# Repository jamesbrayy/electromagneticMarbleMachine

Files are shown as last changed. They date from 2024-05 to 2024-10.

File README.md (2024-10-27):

# electromagneticMarbleMachine
 
a marble machine with a five-stage coil gun to accelerate the marbles.

optimised for ~300V charges (225 J) but capable of up to 405V to give a 10% safety margin (410.0625 J).

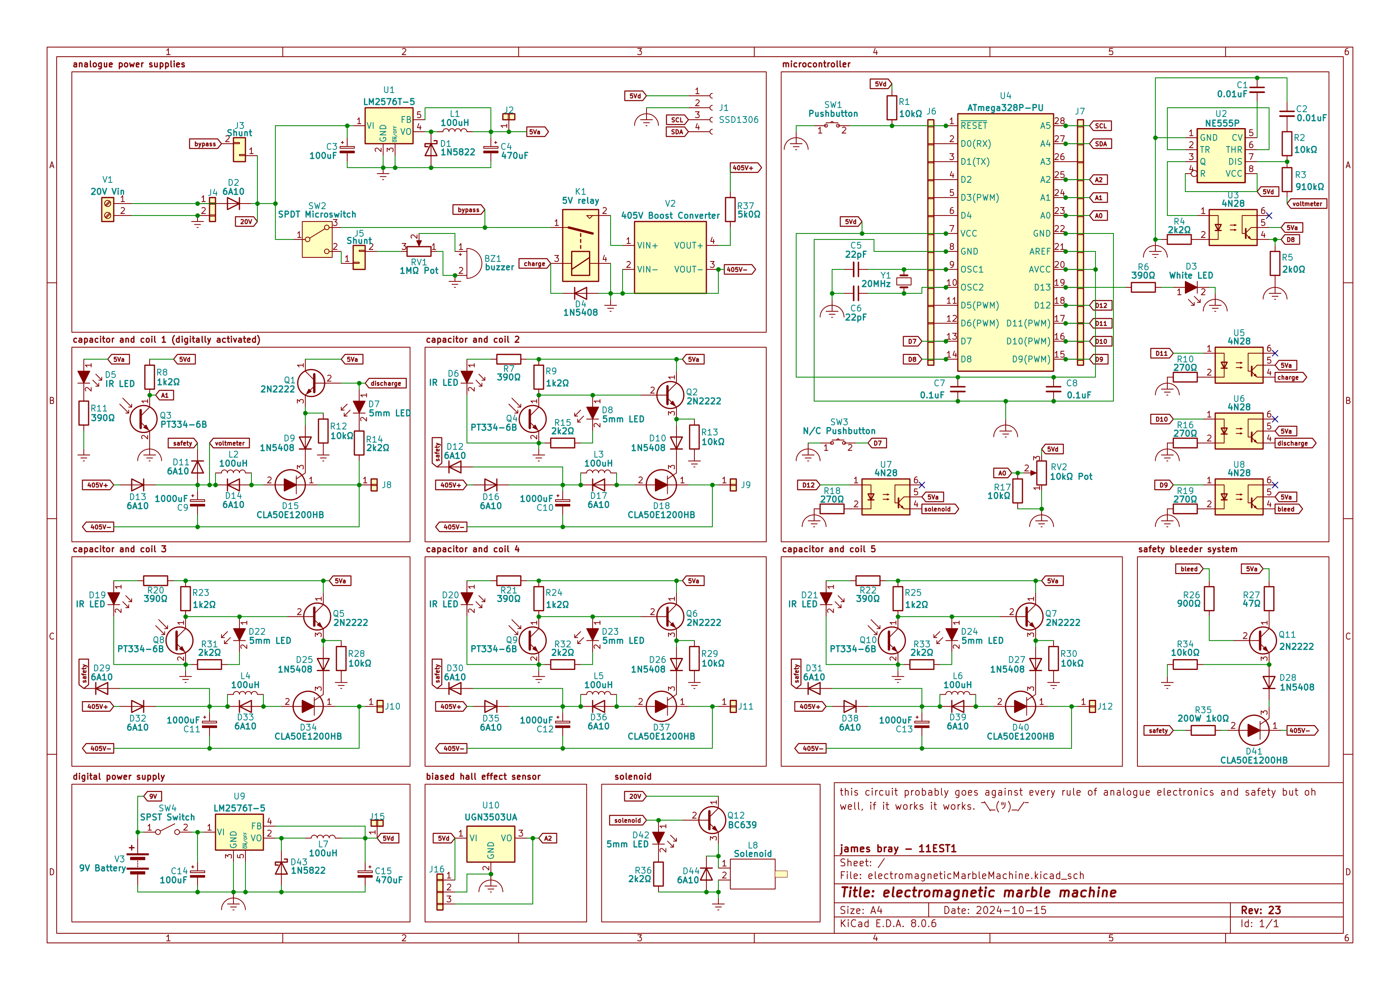
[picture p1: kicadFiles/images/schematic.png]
schematic image

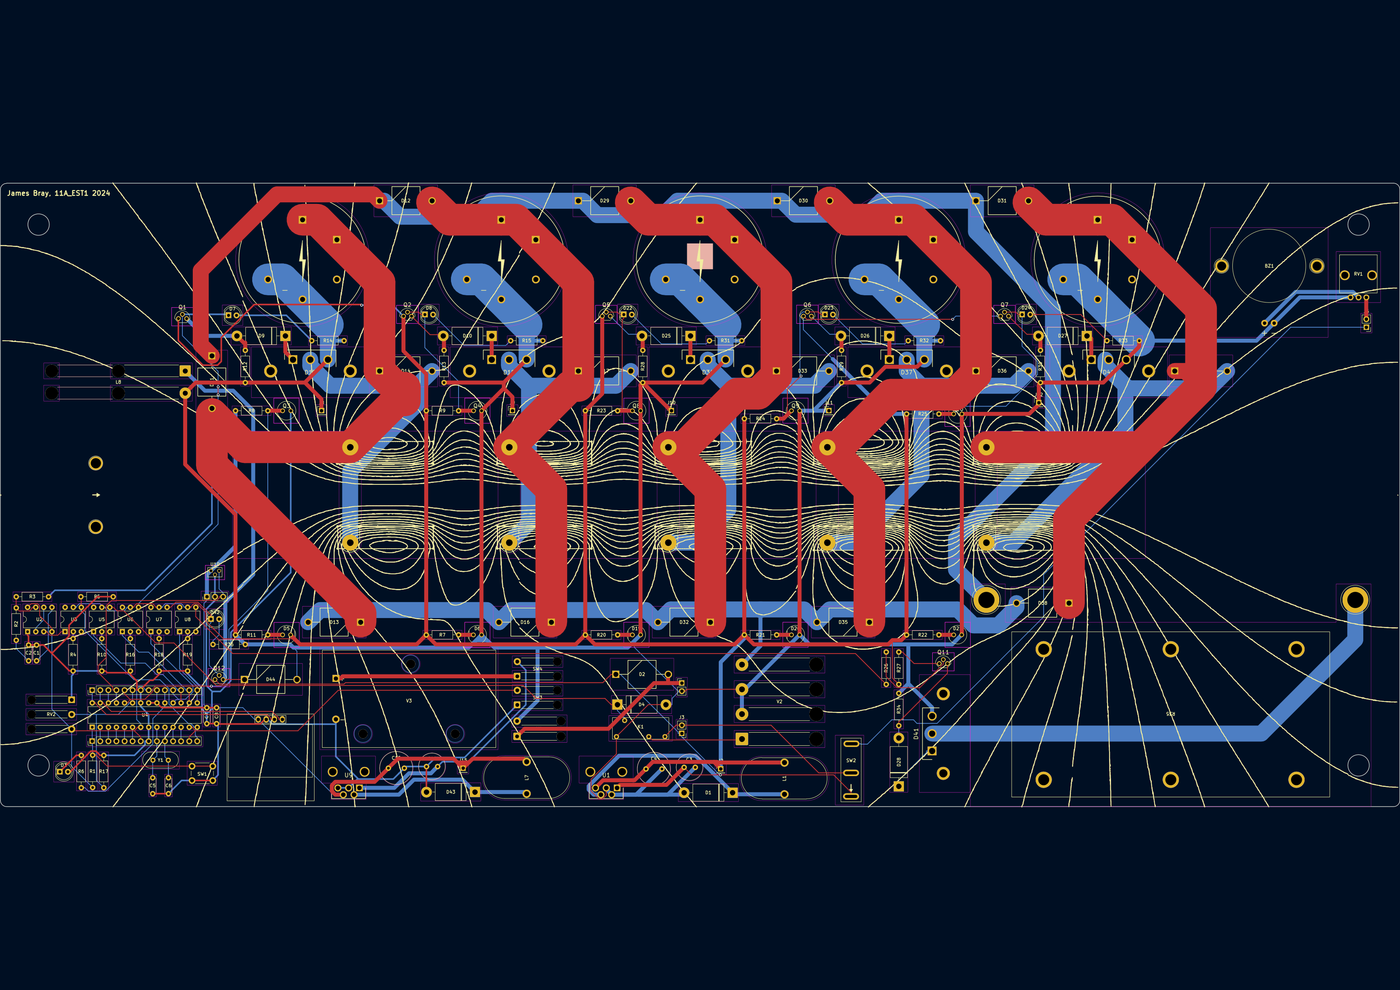
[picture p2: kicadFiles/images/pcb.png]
pcb image


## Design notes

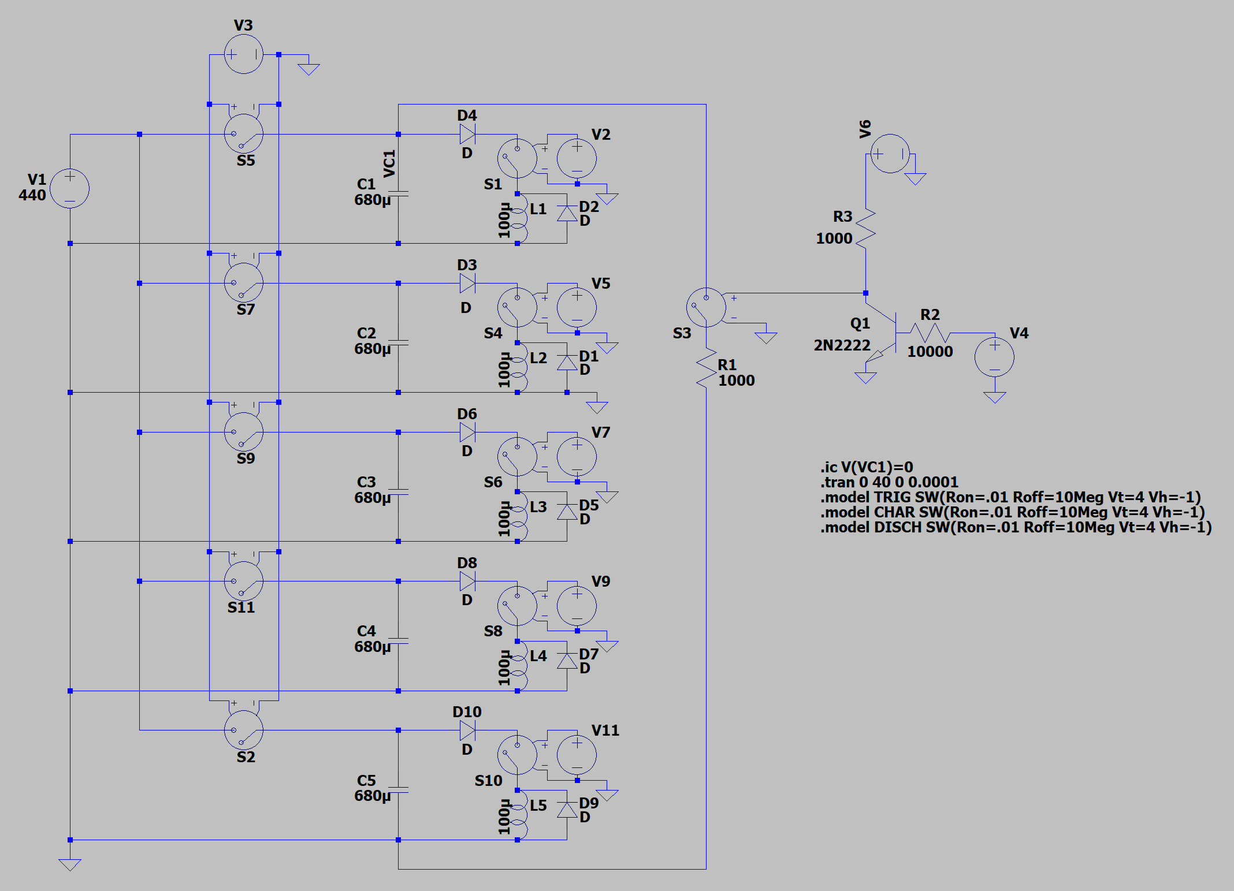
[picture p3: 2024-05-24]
simulationFiles/ltspice files/schematicSPICE.png

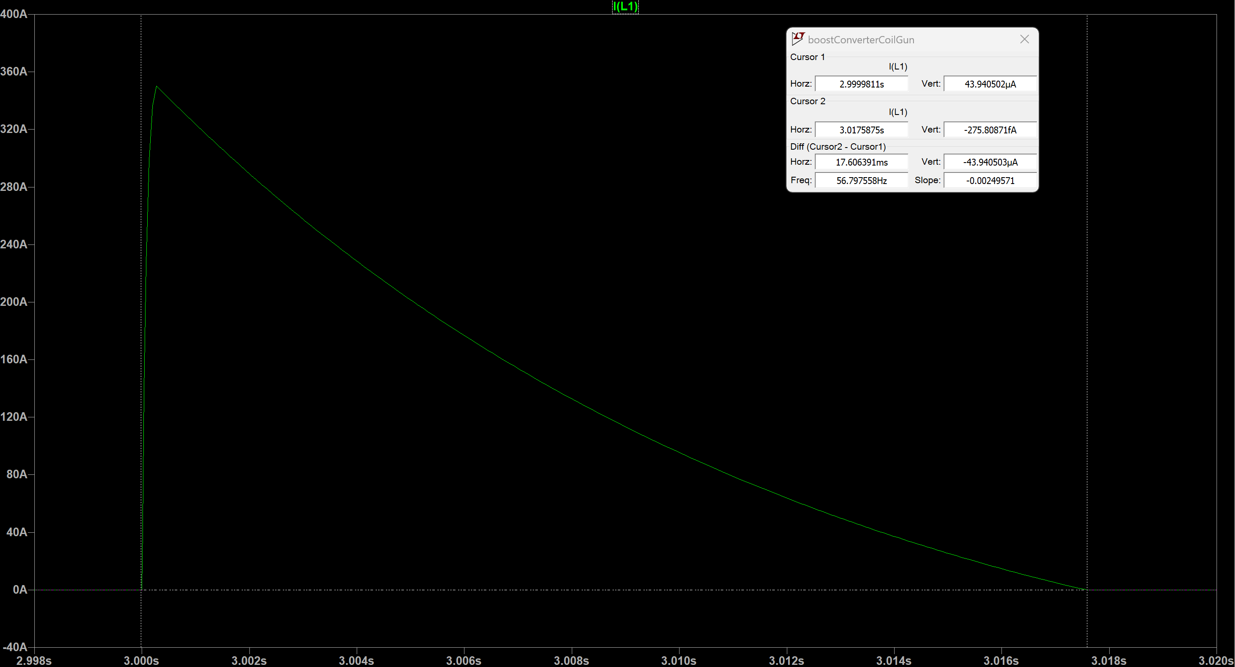
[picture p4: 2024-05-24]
simulationFiles/ltspice files/inductorPulse.png

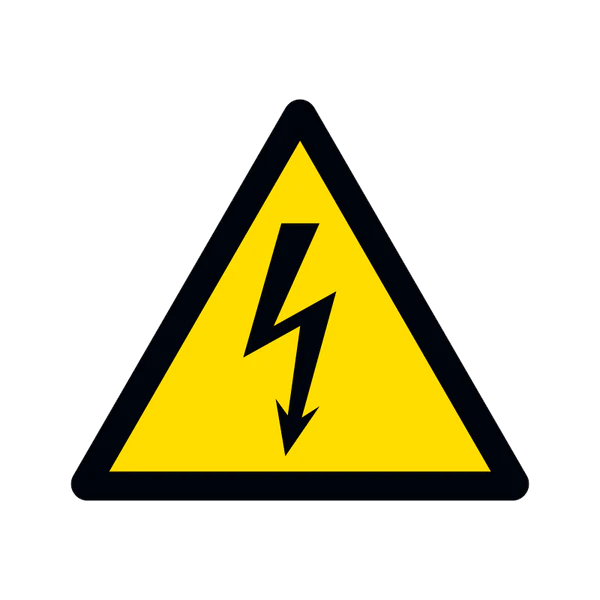
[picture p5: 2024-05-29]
simulationFiles/other random stuff/ruhRohRaggy.png

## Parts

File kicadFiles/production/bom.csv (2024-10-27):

Designator | Footprint | Quantity | Value | LCSC Part #
BZ1 | Buzzer | 1 | buzzer
C1, C2 | C_Disc_D4.3mm_W1.9mm_P5.00mm | 2 | 0.01uF
C10, C11, C12, C13, C9 | officialCAP | 5 | 1000uF
C14, C3 | C_Radial_D8.0mm_H11.5mm_P3.50mm | 2 | 100uF
C15, C4 | C_Radial_D10.0mm_H12.5mm_P5.00mm | 2 | 470uF
C5, C6 | C_Disc_D4.3mm_W1.9mm_P5.00mm | 2 | 22pF
C7, C8 | C_Disc_D4.3mm_W1.9mm_P5.00mm | 2 | 0.1uF
D1, D43 | D_DO-201AD_P15.24mm_Horizontal | 2 | 1N5822
D10, D25, D26, D27, D28, D4, D9 | D_DO-201AD_P15.24mm_Horizontal | 7 | 1N5408
D11, D12, D13, D14, D16, D17, D2, D29, D30, D31, D32, D33, D35, D36, D38, D39, D44 | DIOAD4425W130L885D885 | 17 | 6A10
D15, D18, D34, D37, D40, D41 | TO546P530X1586X2594-3P | 6 | CLA50E1200HB
D19, D20, D21, D5, D6 | QED234 | 5 | IR LED | 151033RS03000
D22, D23, D24, D42, D7, D8 | LED_D5.0mm | 6 | 5mm LED | 151033RS03000
D3 | LED_D5.0mm | 1 | White LED | 151033RS03000
J1 | 128x64OLED | 1 | SSD1306
J10, J11, J12, J15, J2, J8, J9 | 1x1 2.54mm header | 7 | ~
J16 | 1x3 2.54mm header | 1 | Conn_01x03_MountingPin
J3, J5 | PinHeader_1x02_P2.54mm_Vertical | 2 | Shunt
J4 | 1x2 2.54mm header | 1 | Conn_01x03_MountingPin
J6, J7 | 1x14 2.54mm header | 2 | Conn_01x14_MountingPin
K1 | 5v relay | 1 | 5V relay
L1, L7 | Inductor | 2 | 100uH
L2, L3, L4, L5, L6 | Coil Socket | 5 | 100uH
L8 | solenoid_WIRED | 1 | Solenoid
Q1, Q11, Q2, Q5, Q6, Q7 | P2N2222A | 6 | 2N2222
Q10, Q3, Q4, Q8, Q9 | PT3346B | 5 | PT334-6B
Q12 | P2N2222A | 1 | BC639
R1, R12, R13, R17, R2, R28, R29, R30 | R_Axial_DIN0207_L6.3mm_D2.5mm_P10.16mm_Horizontal | 8 | 10kΩ
R10, R16, R18, R19 | R_Axial_DIN0207_L6.3mm_D2.5mm_P10.16mm_Horizontal | 4 | 270Ω
R11, R20, R21, R22, R6, R7 | R_Axial_DIN0207_L6.3mm_D2.5mm_P10.16mm_Horizontal | 6 | 390Ω
R14, R15, R31, R32, R33, R36, R4 | R_Axial_DIN0207_L6.3mm_D2.5mm_P10.16mm_Horizontal | 7 | 2k2Ω
R23, R24, R25, R8, R9 | R_Axial_DIN0207_L6.3mm_D2.5mm_P10.16mm_Horizontal | 5 | 1k2Ω
R26 | R_Axial_DIN0207_L6.3mm_D2.5mm_P10.16mm_Horizontal | 1 | 900Ω
R27 | R_Axial_DIN0207_L6.3mm_D2.5mm_P10.16mm_Horizontal | 1 | 47Ω
R3 | R_Axial_DIN0207_L6.3mm_D2.5mm_P10.16mm_Horizontal | 1 | 910kΩ
R34 | R_Axial_DIN0207_L6.3mm_D2.5mm_P10.16mm_Horizontal | 1 | 10k0Ω
R35 | 200W Resistor | 1 | 200W 1k0Ω
R5 | R_Axial_DIN0207_L6.3mm_D2.5mm_P10.16mm_Horizontal | 1 | 2k0Ω
RV1 | potentiometer | 1 | 1MΩ Pot
RV2 | potentiometerOFFBOARD | 1 | 10kΩ Pot
SW1 | SW_PUSH_6mm | 1 | Pushbutton
SW2 | microswitch | 1 | SPDT Microswitch
SW3 | button_or_keyswitch | 1 | N/C Pushbutton
SW4 | button_or_keyswitch | 1 | SPST Switch
U1, U9 | TO170P483X1016X1611-5P | 2 | LM2576T-5
U10 | UGN3503UA | 1 | UGN3503UA
U2 | DIP-8_W7.62mm | 1 | NE555P
U3, U5, U6, U7, U8 | DIP-6_W7.62mm | 5 | 4N28
U4 | DIP-28_W7.62mm | 1 | ATmega328P-PU
V1 | 20Vin | 1 | 20V Vin
V2 | 405Vin | 1 | 405V Boost Converter
V3 | 9V Battery Holder | 1 | 9V Battery
Y1 | Crystal_HC49-U_Vertical | 1 | 20MHz

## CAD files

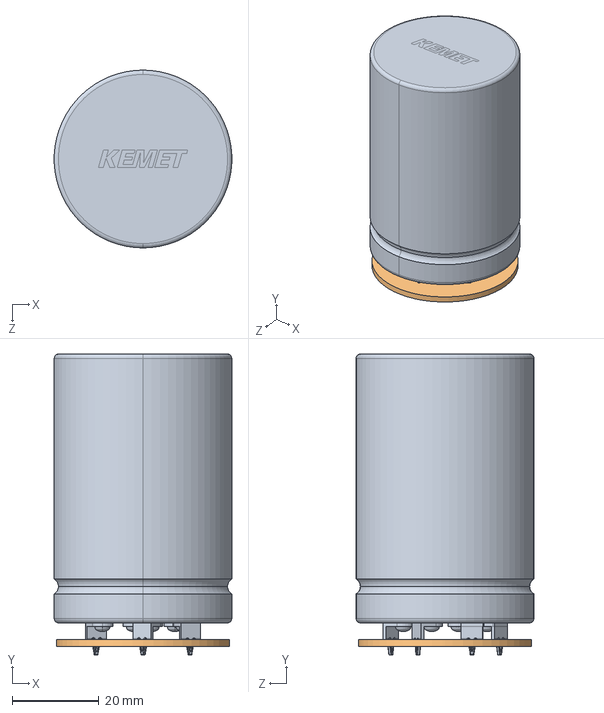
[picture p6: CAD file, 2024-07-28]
solidworksFiles/capacitorAssembly.SLDASM
41.0 x 69.4 x 41.0 mm
capacitorFootprintPart
capacitorPart

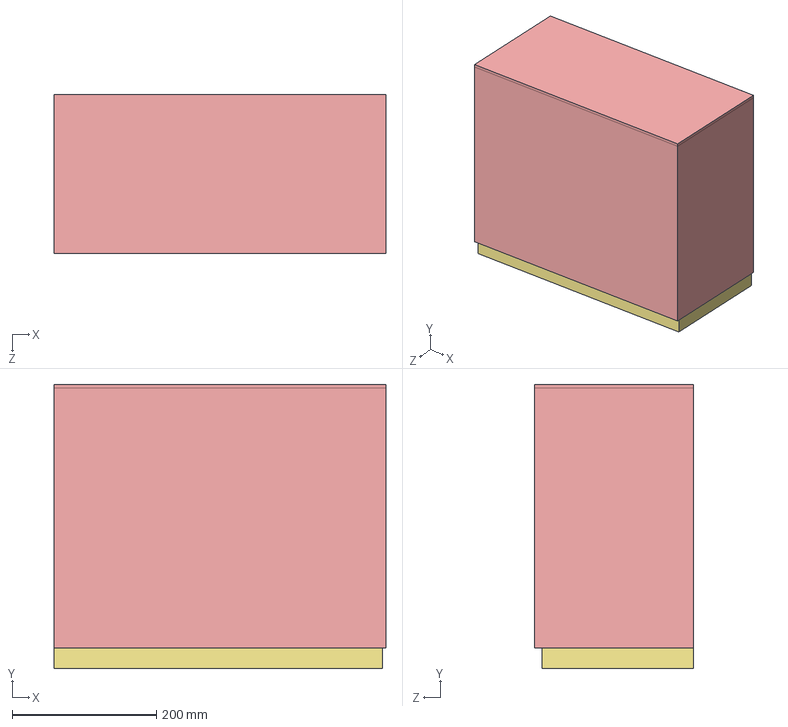
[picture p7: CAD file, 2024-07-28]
solidworksFiles/marbleMachineAssembly.SLDASM
460.0 x 394.0 x 220.0 mm
base
pcbPart
casePart
marblePart
spacerPart x 4
coilPart x 5
tubePart

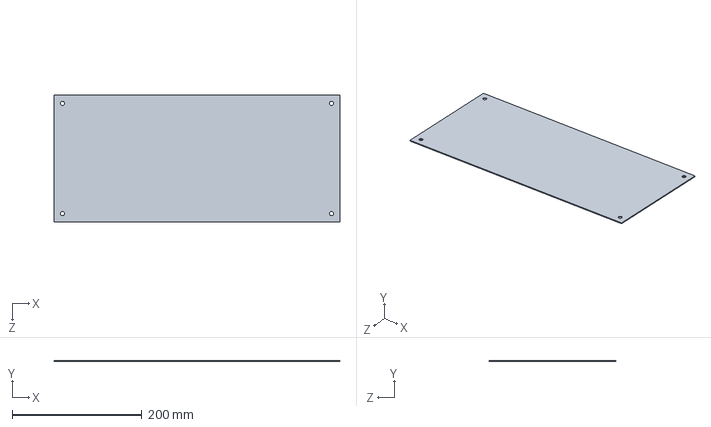
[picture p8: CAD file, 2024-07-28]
solidworksFiles/pcbPart.SLDPRT
441.0 x 1.60 x 196.0 mm

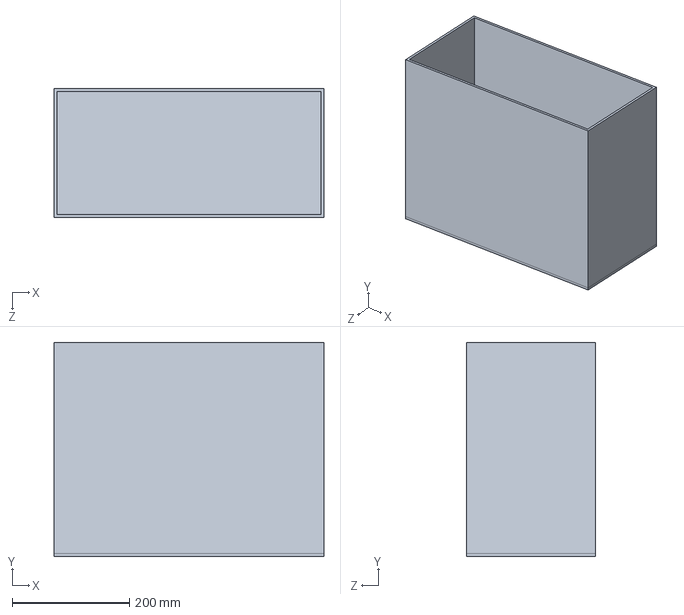
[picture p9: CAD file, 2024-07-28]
solidworksFiles/casePart.SLDPRT
460.0 x 365.0 x 220.0 mm

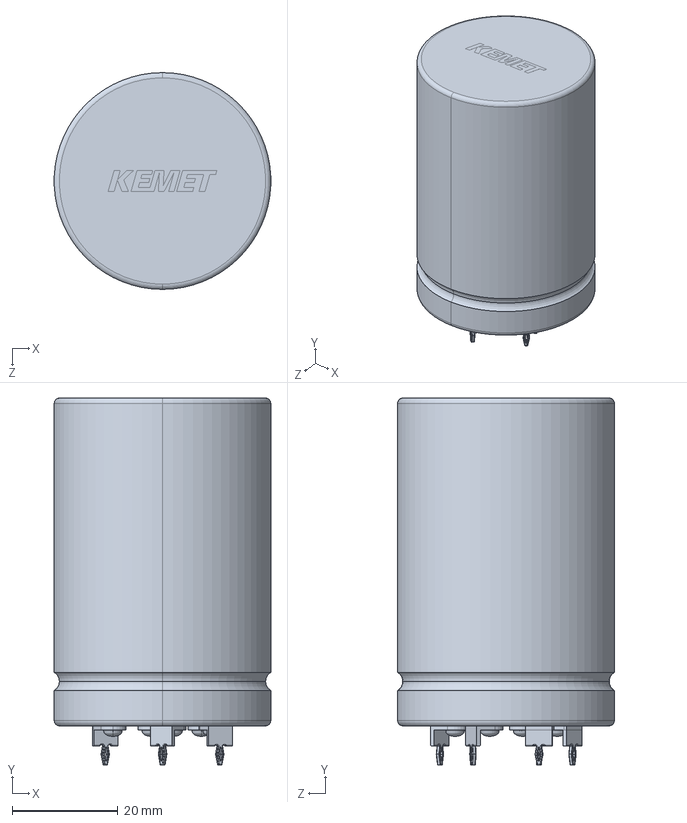
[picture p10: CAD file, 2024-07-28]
solidworksFiles/capacitorPart.SLDPRT
41.0 x 69.4 x 41.0 mm

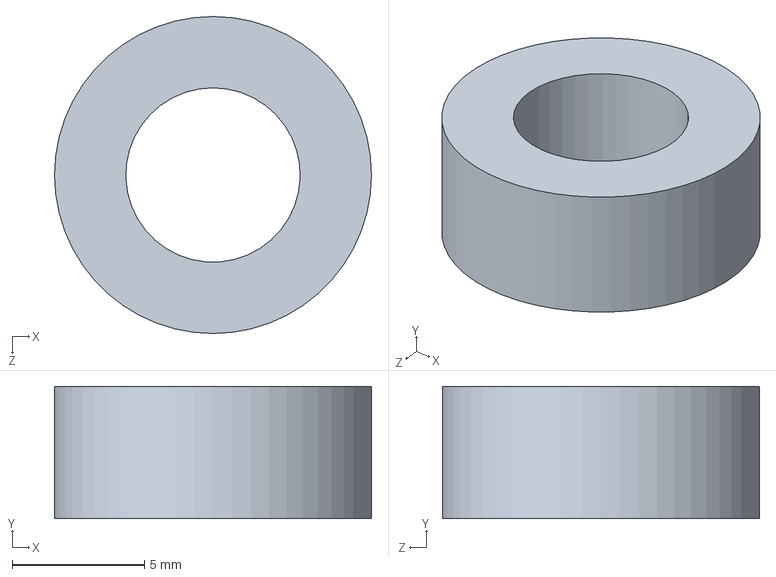
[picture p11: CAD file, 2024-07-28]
solidworksFiles/spacerPart.SLDPRT
12.0 x 5.00 x 12.0 mm

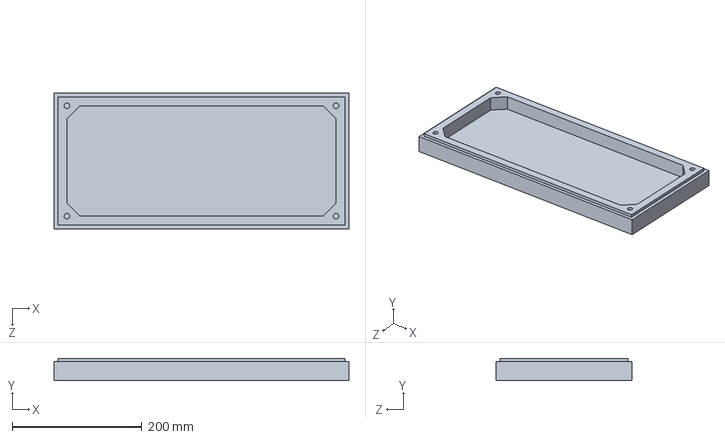
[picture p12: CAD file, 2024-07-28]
solidworksFiles/base.SLDPRT
455.0 x 34.0 x 210.0 mm

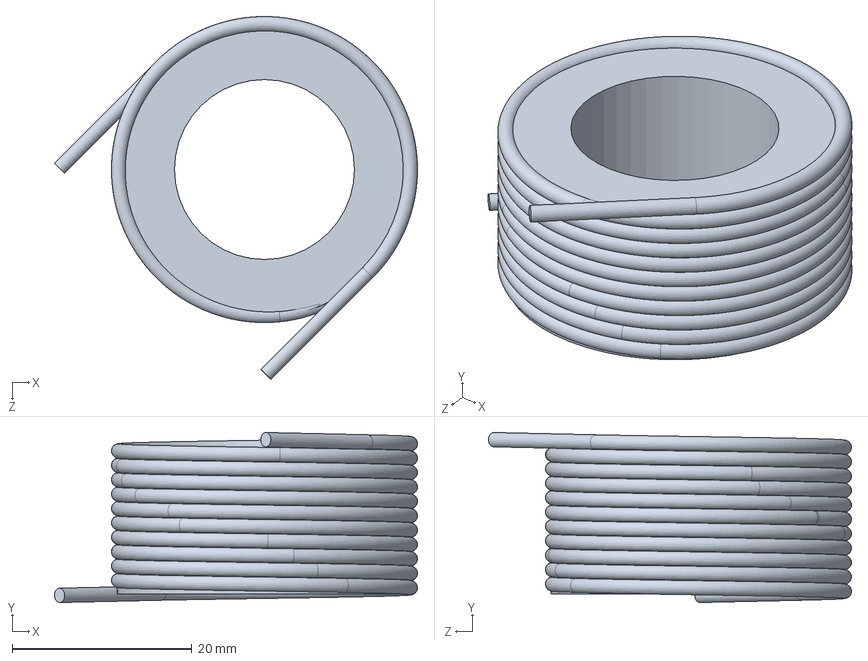
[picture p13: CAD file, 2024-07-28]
solidworksFiles/coilPart.SLDPRT
40.3 x 18.9 x 40.4 mm

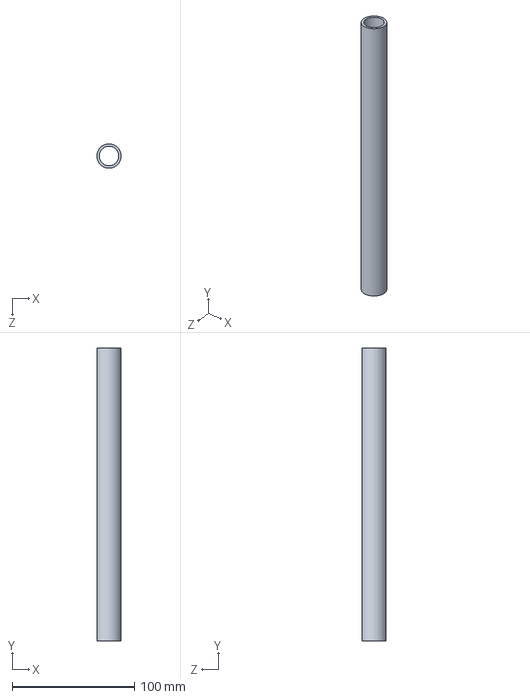
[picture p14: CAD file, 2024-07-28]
solidworksFiles/tubePart.SLDPRT
20.0 x 240.0 x 20.0 mm

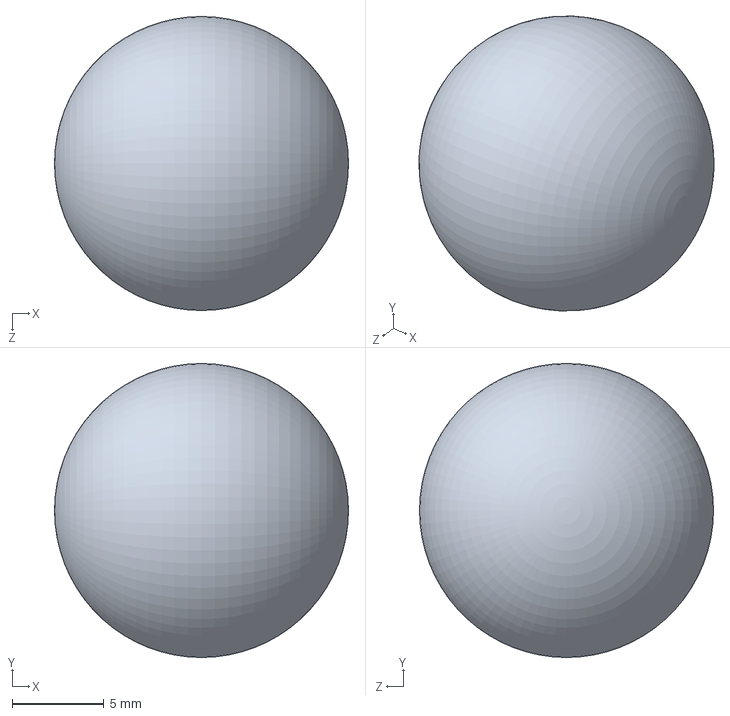
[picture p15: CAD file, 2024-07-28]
solidworksFiles/marblePart.SLDPRT
16.0 x 16.0 x 16.0 mm

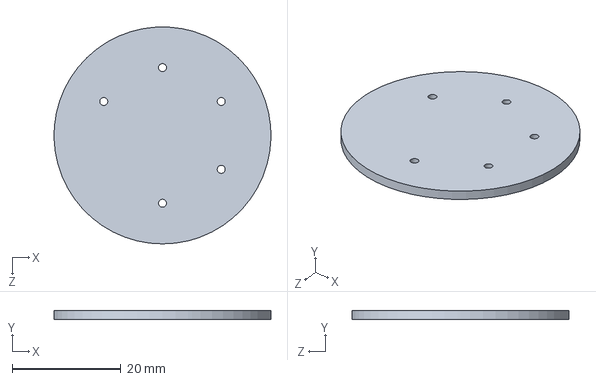
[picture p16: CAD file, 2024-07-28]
solidworksFiles/capacitorFootprintPart.SLDPRT
40.0 x 1.60 x 40.0 mm

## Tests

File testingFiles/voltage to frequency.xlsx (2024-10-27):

time | freq (Hz) | voltage (V)
0 | 876.71 | 363.25 | 23:54:56.780 -> 767.86 | 23:54:56.780 | 767.86 | 23:54:50 | KEEP
10 | 866.32 | 352.71 | 23:54:56.970 -> 768.75 | 23:54:56.970 | 768.75 | 23:54:50 | DELETE
20 | 855.48 | 340.17 | 23:54:57.159 -> 768.86 | 23:54:57.159 | 768.86 | 23:54:50 | DELETE
30 | 845.09 | 328.43 | 23:54:57.253 -> 768.90 | 23:54:57.253 | 768.90 | 23:54:50 | DELETE
40 | 833.94 | 317.79 | 23:54:57.395 -> 768.82 | 23:54:57.395 | 768.82 | 23:54:50 | DELETE
50 | 822.11 | 307.36 | 23:54:57.490 -> 768.79 | 23:54:57.490 | 768.79 | 23:54:50 | DELETE
60 | 810.54 | 296.92 | 23:54:57.632 -> 768.71 | 23:54:57.632 | 768.71 | 23:54:50 | DELETE
70 | 800 | 287.39 | 23:54:57.726 -> 768.64 | 23:54:57.726 | 768.64 | 23:54:50 | DELETE
80 | 788.33 | 278.96 | 23:54:57.820 -> 768.60 | 23:54:57.820 | 768.60 | 23:54:50 | DELETE
90 | 777.3 | 270.03 | 23:54:57.961 -> 768.49 | 23:54:57.961 | 768.49 | 23:54:50 | DELETE
100 | 765.84 | 261.6 | 23:54:58.056 -> 768.42 | 23:54:58.056 | 768.42 | 23:54:50 | DELETE
110 | 754.79 | 252.6 | 23:54:58.198 -> 768.34 | 23:54:58.198 | 768.34 | 23:54:50 | DELETE
120 | 743.67 | 245.1 | 23:54:58.292 -> 768.23 | 23:54:58.292 | 768.23 | 23:54:50 | DELETE
130 | 732.23 | 236.9 | 23:54:58.387 -> 768.12 | 23:54:58.387 | 768.12 | 23:54:50 | DELETE
140 | 720.72 | 228.9 | 23:54:58.528 -> 767.98 | 23:54:58.528 | 767.98 | 23:54:50 | DELETE
150 | 697.62 | 221.3 | 23:54:58.718 -> 767.83 | 23:54:58.718 | 767.83 | 23:54:50 | DELETE
160 | 697.08 | 214 | 23:54:58.814 -> 767.53 | 23:54:58.814 | 767.53 | 23:54:50 | DELETE
170 | 685.9 | 207.4 | 23:54:58.956 -> 767.39 | 23:54:58.956 | 767.39 | 23:54:50 | DELETE
180 | 674.02 | 200 | 23:54:59.051 -> 767.24 | 23:54:59.051 | 767.24 | 23:54:50 | DELETE
190 | 662.25 | 194.3 | 23:54:59.145 -> 767.02 | 23:54:59.145 | 767.02 | 23:54:50 | DELETE
200 | 650.94 | 188.3 | 23:54:59.288 -> 766.83 | 23:54:59.288 | 766.83 | 23:54:50 | DELETE
210 | 628.36 | 182.2 | 23:54:59.383 -> 766.69 | 23:54:59.383 | 766.69 | 23:54:50 | DELETE
220 | 627.87 | 176.5 | 23:54:59.621 -> 766.28 | 23:54:59.621 | 766.28 | 23:55:50 | KEEP
230 | 616.93 | 170.7 | 23:54:59.716 -> 766.14 | 23:54:59.716 | 766.14 | 23:55:50 | DELETE
240 | 605.21 | 165.5 | 23:54:59.858 -> 765.95 | 23:54:59.858 | 765.95 | 23:55:50 | DELETE
250 | 593.96 | 160.1 | 23:55:00.046 -> 765.84 | 23:55:00.046 | 765.84 | 23:55:00 | KEEP
260 | 582.88 | 155.2 | 23:55:00.141 -> 765.59 | 23:55:00.141 | 765.59 | 23:55:00 | DELETE
270 | 560.7 | 150.3 | 23:55:00.282 -> 765.48 | 23:55:00.282 | 765.48 | 23:55:00 | DELETE
280 | 560.2 | 145.9 | 23:55:00.377 -> 765.37 | 23:55:00.377 | 765.37 | 23:55:00 | DELETE
290 | 549.49 | 141.2 | 23:55:00.520 -> 765.29 | 23:55:00.520 | 765.29 | 23:55:00 | DELETE
300 | 538.12 | 136.7 | 23:55:00.615 -> 765.18 | 23:55:00.615 | 765.18 | 23:55:00 | DELETE
310 | 527.29 | 132.6 | 23:55:00.710 -> 765.07 | 23:55:00.710 | 765.07 | 23:55:00 | DELETE
320 | 516.78 | 128.4 | 23:55:00.852 -> 764.93 | 23:55:00.852 | 764.93 | 23:55:00 | DELETE
330 | 496.29 | 124.4 | 23:55:00.946 -> 764.82 | 23:55:00.946 | 764.82 | 23:55:00 | DELETE
340 | 495.59 | 120.5 | 23:55:01.041 -> 764.71 | 23:55:01.041 | 764.71 | 23:55:00 | DELETE
350 | 484.79 | 116.9 | 23:55:01.183 -> 764.56 | 23:55:01.183 | 764.56 | 23:55:00 | DELETE
360 | 474.86 | 113.2 | 23:55:01.277 -> 764.45 | 23:55:01.277 | 764.45 | 23:55:00 | DELETE
370 | 464.64 | 109.6 | 23:55:01.420 -> 764.34 | 23:55:01.420 | 764.34 | 23:55:00 | DELETE
380 | 454.73 | 106.3 | 23:55:01.515 -> 764.23 | 23:55:01.515 | 764.23 | 23:55:00 | DELETE
390 | 435.09 | 103 | 23:55:01.610 -> 764.09 | 23:55:01.610 | 764.09 | 23:55:00 | DELETE
400 | 434.62 | 100 | 23:55:01.752 -> 763.98 | 23:55:01.752 | 763.98 | 23:55:00 | DELETE
410 | 424.66 | 96.9 | 23:55:01.846 -> 763.83 | 23:55:01.846 | 763.83 | 23:55:00 | DELETE
420 | 415.14 | 93.8 | 23:55:01.987 -> 763.69 | 23:55:01.987 | 763.69 | 23:55:00 | DELETE
430 | 405.68 | 91 | 23:55:02.082 -> 763.58 | 23:55:02.082 | 763.58 | 23:55:00 | DELETE
440 | 396.59 | 88.4 | 23:55:02.177 -> 763.47 | 23:55:02.177 | 763.47 | 23:55:00 | DELETE
450 | 387.61 | 85.5 | 23:55:02.319 -> 763.36 | 23:55:02.319 | 763.36 | 23:55:00 | DELETE
460 | 379.11 | 83.1 | 23:55:02.414 -> 763.21 | 23:55:02.414 | 763.21 | 23:55:00 | DELETE
470 | 378.69 | 80.4 | 23:55:02.556 -> 763.14 | 23:55:02.556 | 763.14 | 23:55:00 | DELETE
480 | 369.87 | 78 | 23:55:02.651 -> 762.96 | 23:55:02.651 | 762.96 | 23:55:00 | DELETE
490 | 360.87 | 75.6 | 23:55:02.841 -> 762.85 | 23:55:02.841 | 762.85 | 23:55:00 | DELETE
500 | 352.33 | 73.3 | 23:55:02.983 -> 762.67 | 23:55:02.983 | 762.67 | 23:55:00 | DELETE
510 | 343.83 | 71 | 23:55:03.077 -> 762.56 | 23:55:03.077 | 762.56 | 23:55:00 | DELETE
520 | 327.7 | 69.1 | 23:55:03.171 -> 762.45 | 23:55:03.171 | 762.45 | 23:55:00 | DELETE
530 | 327.33 | 66.9 | 23:55:03.314 -> 762.30 | 23:55:03.314 | 762.30 | 23:55:00 | DELETE
540 | 319.54 | 65.1 | 23:55:03.408 -> 762.20 | 23:55:03.408 | 762.20 | 23:55:00 | DELETE
550 | 311.93 | 63.2 | 23:55:03.502 -> 762.09 | 23:55:03.502 | 762.09 | 23:55:00 | DELETE
560 | 303.98 | 61.4 | 23:55:03.643 -> 761.98 | 23:55:03.643 | 761.98 | 23:55:00 | DELETE
570 | 296.43 | 59.5 | 23:55:03.738 -> 761.87 | 23:55:03.738 | 761.87 | 23:55:00 | DELETE
580 | 281.8 | 57.6 | 23:55:03.880 -> 761.76 | 23:55:03.880 | 761.76 | 23:55:00 | DELETE
590 | 281.47 | 55.8 | 23:55:03.975 -> 761.65 | 23:55:03.975 | 761.65 | 23:55:00 | DELETE
600 | 274.28 | 54.3 | 23:55:04.070 -> 761.54 | 23:55:04.070 | 761.54 | 23:55:00 | DELETE
610 | 267.54 | 52.5 | 23:55:04.213 -> 761.43 | 23:55:04.213 | 761.43 | 23:55:00 | DELETE
620 | 260.87 | 51.2 | 23:55:04.308 -> 761.29 | 23:55:04.308 | 761.29 | 23:55:00 | DELETE
630 | 254.01 | 49.8 | 23:55:04.449 -> 761.18 | 23:55:04.449 | 761.18 | 23:55:00 | DELETE
640 | 241.08 | 48.2 | 23:55:04.544 -> 761.11 | 23:55:04.544 | 761.11 | 23:55:00 | DELETE
650 | 240.8 | 46.7 | 23:55:04.638 -> 761.00 | 23:55:04.638 | 761.00 | 23:55:00 | DELETE
660 | 234.58 | 45.4 | 23:55:04.875 -> 760.93 | 23:55:04.875 | 760.93 | 23:55:00 | DELETE
670 | 228.33 | 43.8 | 23:55:04.969 -> 760.75 | 23:55:04.969 | 760.75 | 23:55:00 | DELETE
680 | 222.37 | 42.6 | 23:55:05.064 -> 760.56 | 23:55:05.064 | 760.56 | 23:55:00 | DELETE
690 | 216.25 | 41.3 | 23:55:05.206 -> 760.46 | 23:55:05.206 | 760.46 | 23:55:00 | DELETE
700 | 205.05 | 40.1 | 23:55:05.301 -> 760.35 | 23:55:05.301 | 760.35 | 23:55:00 | DELETE
710 | 199.96 | 39.2 | 23:55:05.395 -> 760.17 | 23:55:05.395 | 760.17 | 23:55:00 | DELETE
720 | 194.11 | 38.1 | 23:55:05.538 -> 760.06 | 23:55:05.538 | 760.06 | 23:55:00 | DELETE
730 | 188.43 | 36.8 | 23:55:05.633 -> 759.91 | 23:55:05.633 | 759.91 | 23:55:00 | DELETE
740 | 182.89 | 35.7 | 23:55:05.775 -> 759.81 | 23:55:05.775 | 759.81 | 23:55:00 | DELETE
750 | 177.41 | 34.7 | 23:55:05.870 -> 759.66 | 23:55:05.870 | 759.66 | 23:55:00 | DELETE
760 | 172.57 | 33.5 | 23:55:05.965 -> 759.59 | 23:55:05.965 | 759.59 | 23:55:00 | DELETE
770 | 167.4 | 32.4 | 23:55:06.107 -> 759.45 | 23:55:06.107 | 759.45 | 23:55:00 | DELETE
780 | 162.26 | 31.4 | 23:55:06.201 -> 759.37 | 23:55:06.201 | 759.37 | 23:55:00 | DELETE
790 | 157.33 | 30.5 | 23:55:06.344 -> 759.27 | 23:55:06.344 | 759.27 | 23:55:00 | DELETE
800 | 152.56 | 29.6 | 23:55:06.439 -> 759.16 | 23:55:06.439 | 759.16 | 23:55:00 | DELETE
810 | 147.8 | 28.7 | 23:55:06.534 -> 759.01 | 23:55:06.534 | 759.01 | 23:55:00 | DELETE
820 | 143.6 | 27.9 | 23:55:06.676 -> 758.87 | 23:55:06.676 | 758.87 | 23:55:00 | DELETE
830 | 139.14 | 27 | 23:55:06.770 -> 758.69 | 23:55:06.770 | 758.69 | 23:55:00 | DELETE
840 | 134.79 | 26.4 | 23:55:06.914 -> 758.47 | 23:55:06.914 | 758.47 | 23:55:00 | DELETE
850 | 130.61 | 25.5 | 23:55:07.008 -> 758.37 | 23:55:07.008 | 758.37 | 23:55:00 | DELETE
860 | 126.49 | 24.8 | 23:55:07.103 -> 758.22 | 23:55:07.103 | 758.22 | 23:55:00 | DELETE
870 | 122.44 | 24 | 23:55:07.245 -> 758.15 | 23:55:07.245 | 758.15 | 23:55:00 | DELETE
880 | 118.54 | 23.2 | 23:55:07.340 -> 758.04 | 23:55:07.340 | 758.04 | 23:55:00 | DELETE
890 | 114.74 | 22.5 | 23:55:07.435 -> 757.90 | 23:55:07.435 | 757.90 | 23:55:00 | DELETE
900 | 111.02 | 21.9 | 23:55:07.672 -> 757.76 | 23:55:07.672 | 757.76 | 23:55:00 | DELETE
910 | 107.82 | 21.2 | 23:55:07.768 -> 757.50 | 23:55:07.768 | 757.50 | 23:55:00 | DELETE
920 | 104.25 | 20.7 | 23:55:07.862 -> 757.32 | 23:55:07.862 | 757.32 | 23:55:00 | DELETE
930 | 100.84 | 20 | 23:55:08.004 -> 757.15 | 23:55:08.004 | 757.15 | 23:55:00 | DELETE
 |  |  | 23:55:08.101 -> 757.04 | 23:55:08.101 | 757.04 | 23:55:00 | DELETE
 |  |  | 23:55:08.243 -> 756.89 | 23:55:08.243 | 756.89 | 23:55:00 | DELETE
 |  |  | 23:55:08.338 -> 756.72 | 23:55:08.338 | 756.72 | 23:55:00 | DELETE
 |  |  | 23:55:08.433 -> 756.57 | 23:55:08.433 | 756.57 | 23:55:00 | DELETE
 |  |  | 23:55:08.575 -> 756.43 | 23:55:08.575 | 756.43 | 23:55:00 | DELETE
 |  |  | 23:55:08.670 -> 756.32 | 23:55:08.670 | 756.32 | 23:55:00 | DELETE
 |  |  | 23:55:08.765 -> 756.18 | 23:55:08.765 | 756.18 | 23:55:00 | DELETE
 |  |  | 23:55:08.907 -> 756.07 | 23:55:08.907 | 756.07 | 23:55:00 | DELETE
 |  |  | 23:55:09.002 -> 755.97 | 23:55:09.002 | 755.97 | 23:55:00 | DELETE
 |  |  | 23:55:09.146 -> 755.79 | 23:55:09.146 | 755.79 | 23:55:00 | DELETE
 |  |  | 23:55:09.240 -> 755.68 | 23:55:09.240 | 755.68 | 23:55:00 | DELETE
 |  |  | 23:55:09.335 -> 755.57 | 23:55:09.335 | 755.57 | 23:55:00 | DELETE
 |  |  | 23:55:09.478 -> 755.43 | 23:55:09.478 | 755.43 | 23:55:00 | DELETE
 |  |  | 23:55:09.573 -> 755.29 | 23:55:09.573 | 755.29 | 23:55:00 | DELETE
 |  |  | 23:55:09.715 -> 755.14 | 23:55:09.715 | 755.14 | 23:55:00 | DELETE
 |  |  | 23:55:09.810 -> 755.00 | 23:55:09.810 | 755.00 | 23:55:00 | DELETE
 |  |  | 23:55:09.905 -> 754.90 | 23:55:09.905 | 754.90 | 23:55:00 | DELETE
 |  |  | 23:55:10.094 -> 754.79 | 23:55:10.094 | 754.79 | 23:55:10 | KEEP
 |  |  | 23:55:10.236 -> 754.61 | 23:55:10.236 | 754.61 | 23:55:10 | DELETE
 |  |  | 23:55:10.331 -> 754.47 | 23:55:10.331 | 754.47 | 23:55:10 | DELETE
 |  |  | 23:55:10.472 -> 754.40 | 23:55:10.472 | 754.40 | 23:55:10 | DELETE
 |  |  | 23:55:10.567 -> 754.29 | 23:55:10.567 | 754.29 | 23:55:10 | DELETE
 |  |  | 23:55:10.661 -> 754.18 | 23:55:10.661 | 754.18 | 23:55:10 | DELETE
 |  |  | 23:55:10.802 -> 754.08 | 23:55:10.802 | 754.08 | 23:55:10 | DELETE
 |  |  | 23:55:10.896 -> 753.97 | 23:55:10.896 | 753.97 | 23:55:10 | DELETE
 |  |  | 23:55:11.038 -> 753.83 | 23:55:11.038 | 753.83 | 23:55:10 | DELETE
 |  |  | 23:55:11.132 -> 753.69 | 23:55:11.132 | 753.69 | 23:55:10 | DELETE
 |  |  | 23:55:11.227 -> 753.58 | 23:55:11.227 | 753.58 | 23:55:10 | DELETE
 |  |  | 23:55:11.369 -> 753.47 | 23:55:11.369 | 753.47 | 23:55:10 | DELETE
 |  |  | 23:55:11.464 -> 753.37 | 23:55:11.464 | 753.37 | 23:55:10 | DELETE
 |  |  | 23:55:11.606 -> 753.22 | 23:55:11.606 | 753.22 | 23:55:10 | DELETE
 |  |  | 23:55:11.701 -> 753.08 | 23:55:11.701 | 753.08 | 23:55:10 | DELETE
 |  |  | 23:55:11.795 -> 752.98 | 23:55:11.795 | 752.98 | 23:55:10 | DELETE
 |  |  | 23:55:12.033 -> 752.83 | 23:55:12.033 | 752.83 | 23:55:10 | DELETE
 |  |  | 23:55:12.128 -> 752.66 | 23:55:12.128 | 752.66 | 23:55:10 | DELETE
 |  |  | 23:55:12.222 -> 752.52 | 23:55:12.222 | 752.52 | 23:55:10 | DELETE
 |  |  | 23:55:12.364 -> 752.37 | 23:55:12.364 | 752.37 | 23:55:10 | DELETE
 |  |  | 23:55:12.459 -> 752.27 | 23:55:12.459 | 752.27 | 23:55:10 | DELETE
 |  |  | 23:55:12.600 -> 752.16 | 23:55:12.600 | 752.16 | 23:55:10 | DELETE
 |  |  | 23:55:12.695 -> 752.02 | 23:55:12.695 | 752.02 | 23:55:10 | DELETE
 |  |  | 23:55:12.790 -> 751.95 | 23:55:12.790 | 751.95 | 23:55:10 | DELETE
 |  |  | 23:55:12.934 -> 751.81 | 23:55:12.934 | 751.81 | 23:55:10 | DELETE
 |  |  | 23:55:13.028 -> 751.63 | 23:55:13.028 | 751.63 | 23:55:10 | DELETE
 |  |  | 23:55:13.123 -> 751.56 | 23:55:13.123 | 751.56 | 23:55:10 | DELETE
 |  |  | 23:55:13.264 -> 751.42 | 23:55:13.264 | 751.42 | 23:55:10 | DELETE
 |  |  | 23:55:13.359 -> 751.31 | 23:55:13.359 | 751.31 | 23:55:10 | DELETE
 |  |  | 23:55:13.500 -> 751.17 | 23:55:13.500 | 751.17 | 23:55:10 | DELETE
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

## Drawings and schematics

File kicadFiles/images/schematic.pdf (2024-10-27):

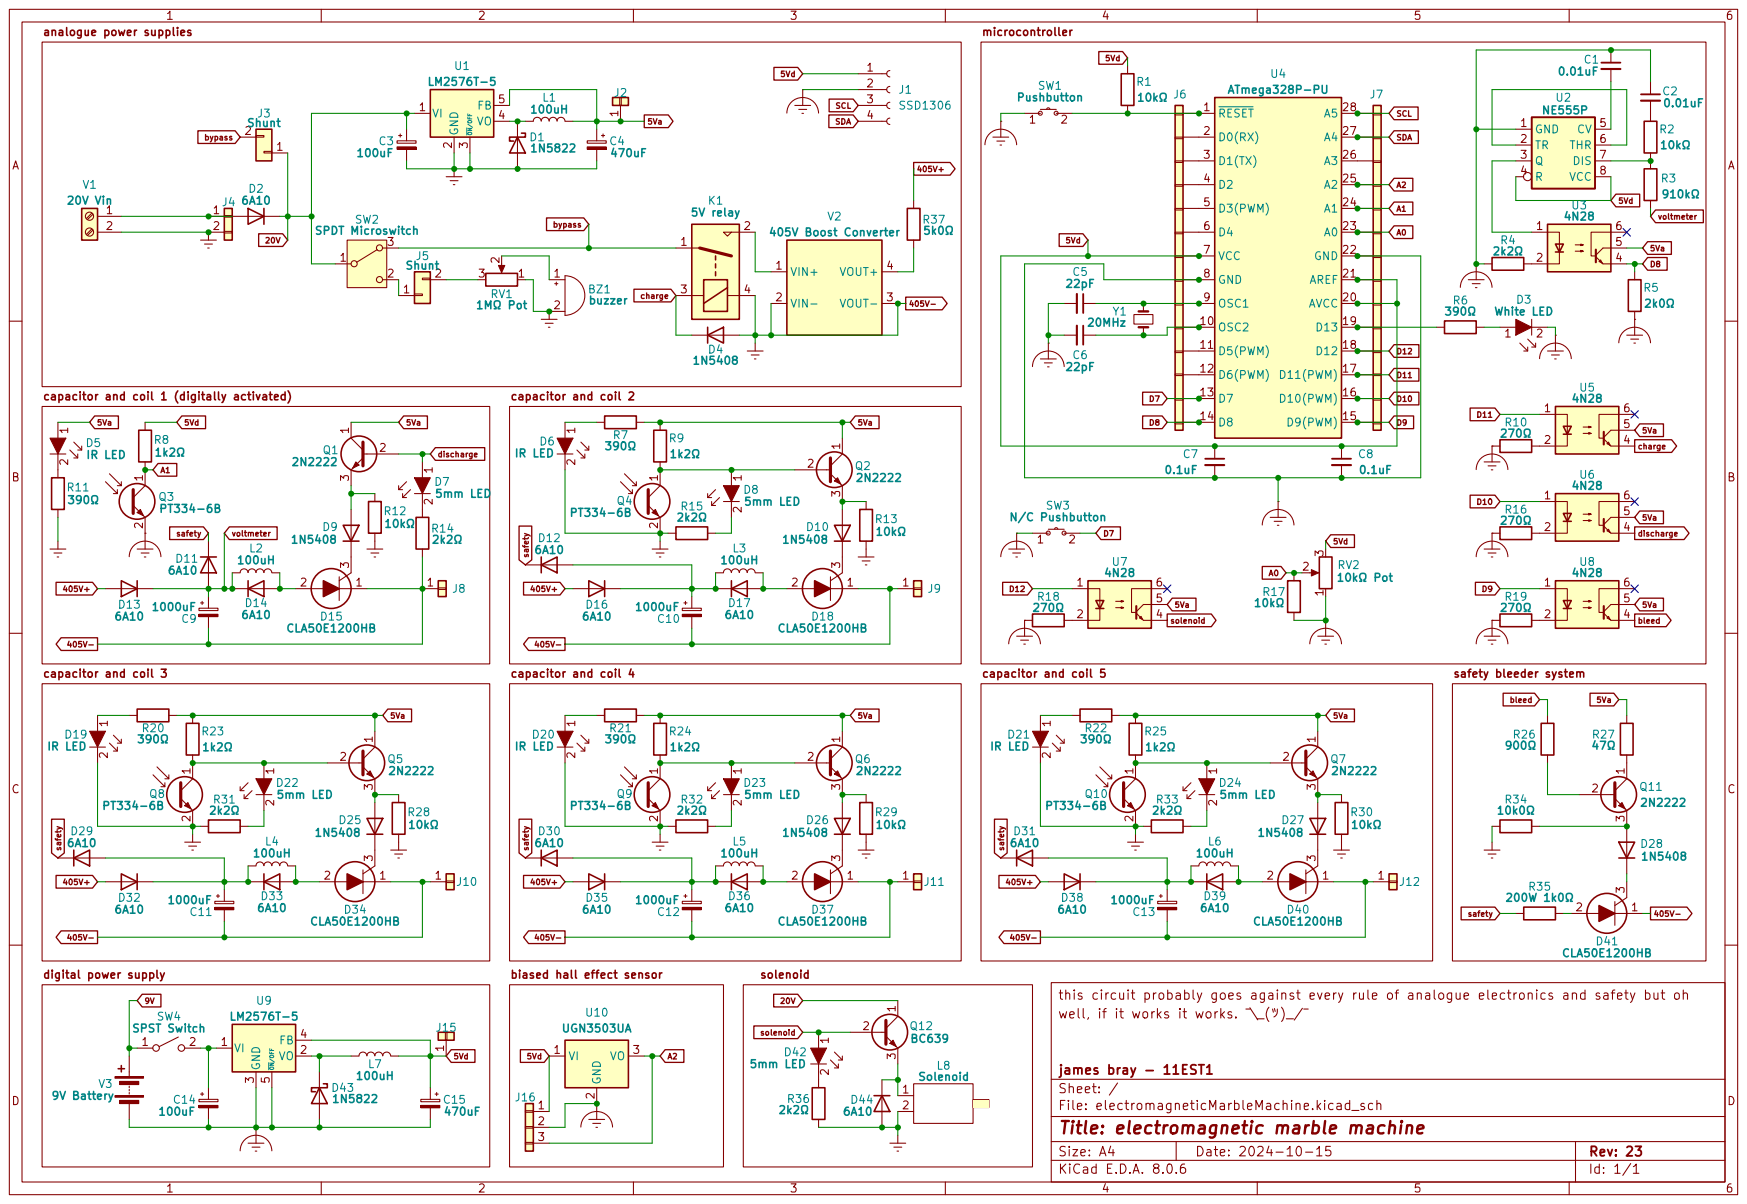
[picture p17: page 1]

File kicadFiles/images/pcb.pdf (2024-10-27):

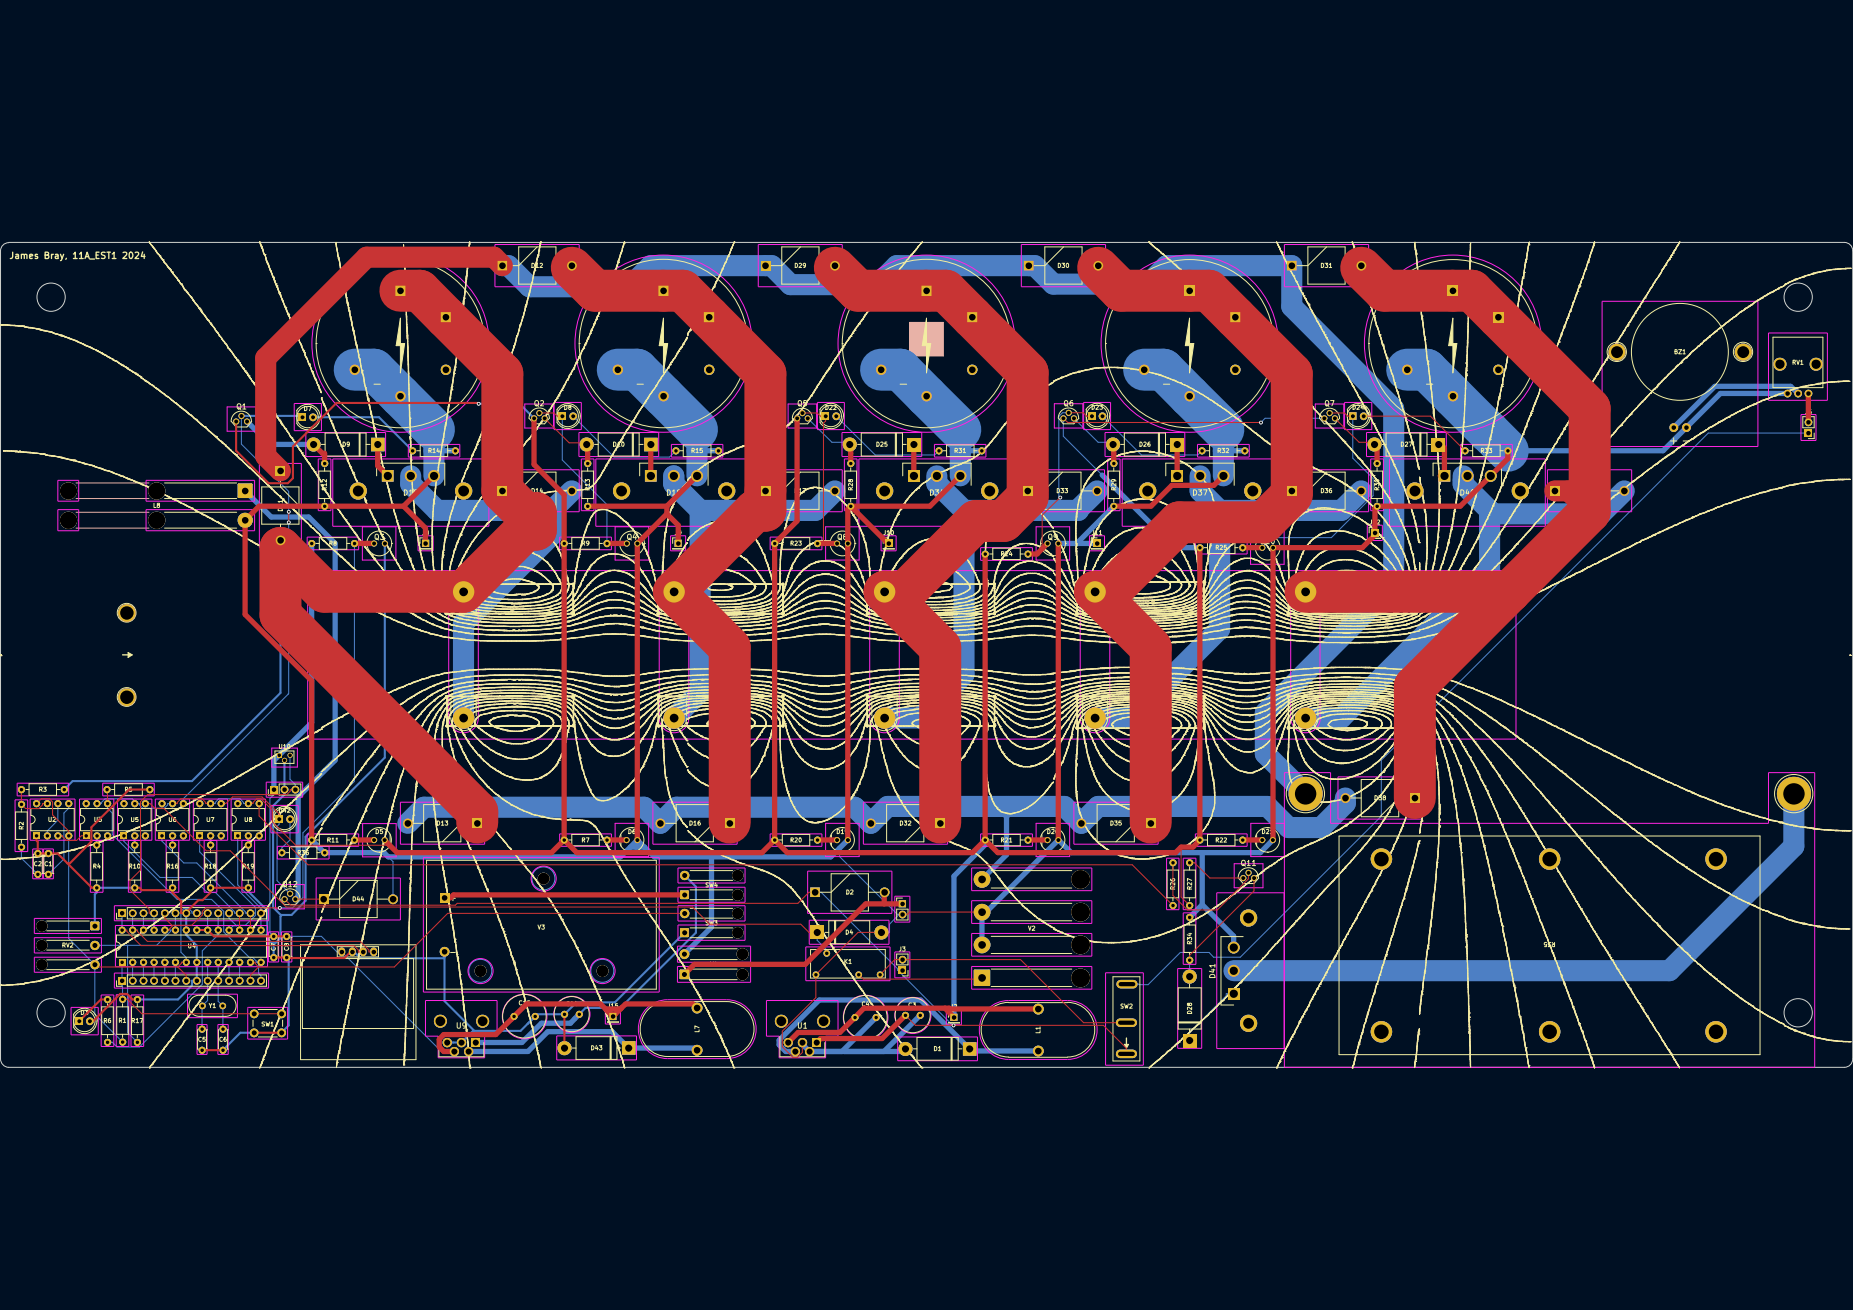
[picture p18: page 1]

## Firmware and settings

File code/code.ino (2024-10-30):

#include <U8g2lib.h>
#include <math.h>
#include <FreqMeasure.h>

// Initialize display with a single font for efficiency
U8G2_SSD1306_128X64_NONAME_F_HW_I2C u8g2(U8G2_R0, -1, A5, A4);

uint16_t capVoltage = 0, setVoltage = 0; // Changed from float to uint16_t
uint16_t frequency = 0; // Changed from float to uint16_t

const uint8_t potentiometer = A0, receiverIR = A1, hallEffect = A2;
const uint8_t buttonPin = 7, bleed = 9, dischargePin = 10, chargePin = 11, solenoidPin = 12, indicatorLED = 13;
const uint8_t debounce = 20, holdTime = 2000;

bool mode = false;
double sum=0;
int count=0;

int hallValue;
int b = 0; // value read from button
int blast = 0; // buffered value of the button's previous state
unsigned long bdown; // time the button was pressed down
unsigned long bup; // time the button was released

#define centreX(text) ((128 - u8g2.getStrWidth(text)) / 2)

void setup() {
  Serial.begin(57600);  // Start serial communication
  FreqMeasure.begin();

  pinMode(bleed, OUTPUT);
  pinMode(buttonPin, INPUT);
  pinMode(chargePin, OUTPUT);
  pinMode(dischargePin, OUTPUT);
  pinMode(indicatorLED, OUTPUT);
  pinMode(solenoidPin, OUTPUT);
  
  digitalWrite(buttonPin, HIGH); // pull-up 20k
  digitalWrite(indicatorLED, LOW);
  
  u8g2.begin();  // Initialize the display
  u8g2.clearBuffer();  // Clear the display buffer
  
  // Set a single font for efficiency
  u8g2.setFont(u8g2_font_profont12_tr);  
  u8g2.setCursor(30, 20);  
  u8g2.print(F("James Bray's"));  
  u8g2.setCursor(1, 40);  
  u8g2.setFont(u8g2_font_profont17_tr);
  u8g2.print(F("Marble Machine"));  
  u8g2.setCursor(34, 60);  
  u8g2.setFont(u8g2_font_profont10_tr);  
  u8g2.print(F("2024 11A_EST1"));  
  u8g2.sendBuffer();  
  delay(3000);  
  u8g2.clearBuffer();  
}

void charging() {
  digitalWrite(chargePin, HIGH);
  u8g2.setFont(u8g2_font_profont12_tr); 
  u8g2.setCursor(centreX("Set Voltage: 000 V"), 25);
  u8g2.print(F("Set Voltage: "));
  u8g2.print(setVoltage);  
  u8g2.print(F(" V"));

  u8g2.setCursor(centreX("Cap Voltage: 000 V"), 40);
  u8g2.print(F("Cap Voltage: "));
  
  if (capVoltage < 20) {
    u8g2.print(F("<20 V"));
  } else {
    u8g2.print(capVoltage);  
    u8g2.print(F(" V"));
  }

  u8g2.setBitmapMode(1);
  u8g2.drawFrame(12, 44, 104, 18);  
  u8g2.drawBox(14, 46, (capVoltage * 100 / setVoltage), 14);  
}

void automatic() {
  digitalWrite(chargePin, LOW);
  discharge();
}

void manual() {
  digitalWrite(chargePin, LOW);
  u8g2.clearBuffer();
  mode = false;
  drawHeader();
  u8g2.setFont(u8g2_font_profont12_tr);
  u8g2.setCursor(centreX("Press the button to"), 26);
  u8g2.print(F("Press the button to"));
  u8g2.setCursor(centreX("manually discharge."), 38);
  u8g2.print(F("manually discharge."));
  u8g2.sendBuffer();

  // Wait until the button is released
  while (digitalRead(buttonPin) == HIGH);

  // Debounce: wait for stable LOW state
  delay(debounce);

  // Check if the button is released (button is LOW)
  if (digitalRead(buttonPin) == LOW) {
    unsigned long startTime = millis(); // Start timer after button release

    while (true) {
      // Wait for the button to be pressed again (HIGH state)
      while (digitalRead(buttonPin) == LOW) {
        // Check if 5 seconds have passed since the button was released
        if (millis() - startTime > 5000) {
          return; // Exit the function after 5 seconds of no input
        }
      }

      // Button pressed, debounce
      delay(debounce);

      // If button is pressed (HIGH state) within 5 seconds, proceed with discharge
      if (digitalRead(buttonPin) == HIGH) {
        discharge(); // Call discharge function
        break;
      }
    }
  }
}


void discharge() {
  for (int8_t i = 3; i > 0; i--) {
    u8g2.clearBuffer();
    drawHeader();
    u8g2.setCursor(20, 25);
    u8g2.setFont(u8g2_font_profont12_tr);
    u8g2.print(F("Discharging in:"));
    u8g2.setCursor(56, 50);
    u8g2.setFont(u8g2_font_profont29_tr);
    u8g2.print(i);
    u8g2.sendBuffer();
    delay(1000);  
  }
  u8g2.clearBuffer();
  drawHeader();
  u8g2.setCursor(16, 42);
  u8g2.setFont(u8g2_font_profont17_tr);
  u8g2.print(F("DISCHARGING"));
  u8g2.sendBuffer();
  digitalWrite(solenoidPin, HIGH);
  while (analogRead(receiverIR) < 512);
  digitalWrite(solenoidPin, LOW);
  digitalWrite(dischargePin, HIGH);
  delay(1000);
  digitalWrite(dischargePin, LOW);
}

void drawHeader() {
  u8g2.setFont(u8g2_font_profont10_tr);
  u8g2.drawLine(0, 12, 128, 12);
  u8g2.setCursor(0, 10);
  u8g2.print(mode ? F("Automatic Mode") : F("Manual Mode"));
  u8g2.setCursor(100, 10);
  u8g2.print(frequency);
}

void checkButton() {
  static enum { IDLE, PRESSED, HELD } buttonState = IDLE;
  b = digitalRead(buttonPin);
  
  switch (buttonState) {
    case IDLE:
      // Detect button press (transition from LOW to HIGH for normally closed)
      if (b == HIGH && (millis() - bup) > debounce) {
        bdown = millis(); // Record when the button was pressed down
        buttonState = PRESSED;
      }
      break;

    case PRESSED:
      // Check if button has been held long enough for a long press
      if (b == HIGH && (millis() - bdown) >= holdTime) {
        manual(); // Trigger the long press action
        buttonState = HELD;
      }
      // If the button is released before holdTime, it's a short press
      else if (b == LOW) {
        if ((millis() - bdown) > debounce) {
          mode = !mode; // Toggle mode on short press
        }
        bup = millis(); // Record the time when the button was released
        buttonState = IDLE;
      }
      break;

    case HELD:
      // Wait for the button to be released after a long press
      if (b == LOW) {
        bup = millis(); // Record when the button was released
        buttonState = IDLE;
      }
      break;
  }

  blast = b; // Update the last button state
}




void loop() {
  static float f;
  delay(10);
  u8g2.clearBuffer();
  
  // Ensure you only calculate frequency after a certain interval
  if (FreqMeasure.available()) {
    // average several reading together
    f = FreqMeasure.read();
    sum = sum + f;
    count = count + 1;
    if (count > 1) {
      frequency = FreqMeasure.countToFrequency(sum / count);
      sum = 0;
      count = 0;
    }
  }

  checkButton();
  drawHeader();
  
  hallValue = analogRead(hallEffect);  

  setVoltage = map(analogRead(potentiometer), 10, 1013, 20, 80) * 5;  
  capVoltage = (uint16_t)(47.05 * exp(0.002425 * frequency)) - 37.87;  
  if (setVoltage > capVoltage) {
    charging();
  } else {
    mode ? automatic() : manual();
  }
  
  u8g2.sendBuffer();
}

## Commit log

2024-05-24 Add schematic.pdf
2024-05-24 Add schematic.png
2024-06-12 add latest femm simulation files
    [simulation calcs.xlsx]
2024-07-28 idk
    idk
    [base.SLDPRT, capacitorAssembly.SLDASM, capacitorFootprintPart.SLDPRT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]
2024-10-27 final PCB added
    a bunch of simulation and KiCad files.
    [base.SLDPRT, bom.csv, capacitorAssembly.SLDASM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]
2024-10-27 assorted files
    an assortment of images and plots of my electronics have been added.
    [bom.csv, designators.csv, electromagneticMarbleMachine.kicad_sch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]
2024-10-30 error fixes
    [electromagneticMarbleMachine.kicad_sch]
